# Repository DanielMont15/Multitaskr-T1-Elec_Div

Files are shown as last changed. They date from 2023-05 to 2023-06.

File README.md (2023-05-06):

## Multitaskr-T1-Elec_Div
# Electronics Division  
ECAD and documentation repository for everything electronics related to Rotational &amp; Controlled Mechanism and transmission system for camera scanner project.

# Abstract
Among the services offered by Multitaskr, a 3D manual scanning of rooms with a camera is performed. With the purpose of improving processes, the automation of this process is proposed by developing a mobile and foldable platform that allows modifying the Pitch and Yaw position (in a range of 360 and -45 to 45, respectively) of the camera via a robotic system with 2 degrees of freedom.

The development considers the use of SCRUM methodology to keep track of the proposed objectives and detected failures; CAD and ECAD software (SolidWorks and Eagle); MATLAB for the design and tuning of the controller; TEC laboratories and other related facilities; as well as testing the system to identify areas of opportunity.

In order to achieve this goal, the process will last 10 weeks and will be divided into areas (Mechanics, Electronics, Control and Manufacturing) with the involvement of 8th semester students in Mechatronics with relevant experience in these areas. The testing phase is intended to ensure the delivery of a product according to the specifications.  

A functional prototype is expected to be delivered with the requirements established in the design process; as well as an "Engineering Manual" with CAD models, research processes, schematics, codes and operation guidelines along with the tests and areas of opportunity identified. 

It has been identified that the system can improve the accuracy and efficiency of the process, benefiting Multitaskr operationally and providing its clients with greater value in the services acquired.

# Objective of this repository
To track and mantain in a single platform all related documents in order to be able to replicate the project if needed. Expect to find:
* Entries to the Engineering Manual on the electronics subdivision and updates to said entries.
* ECAD files of the desgined circuits
* Diagrams/Drawings

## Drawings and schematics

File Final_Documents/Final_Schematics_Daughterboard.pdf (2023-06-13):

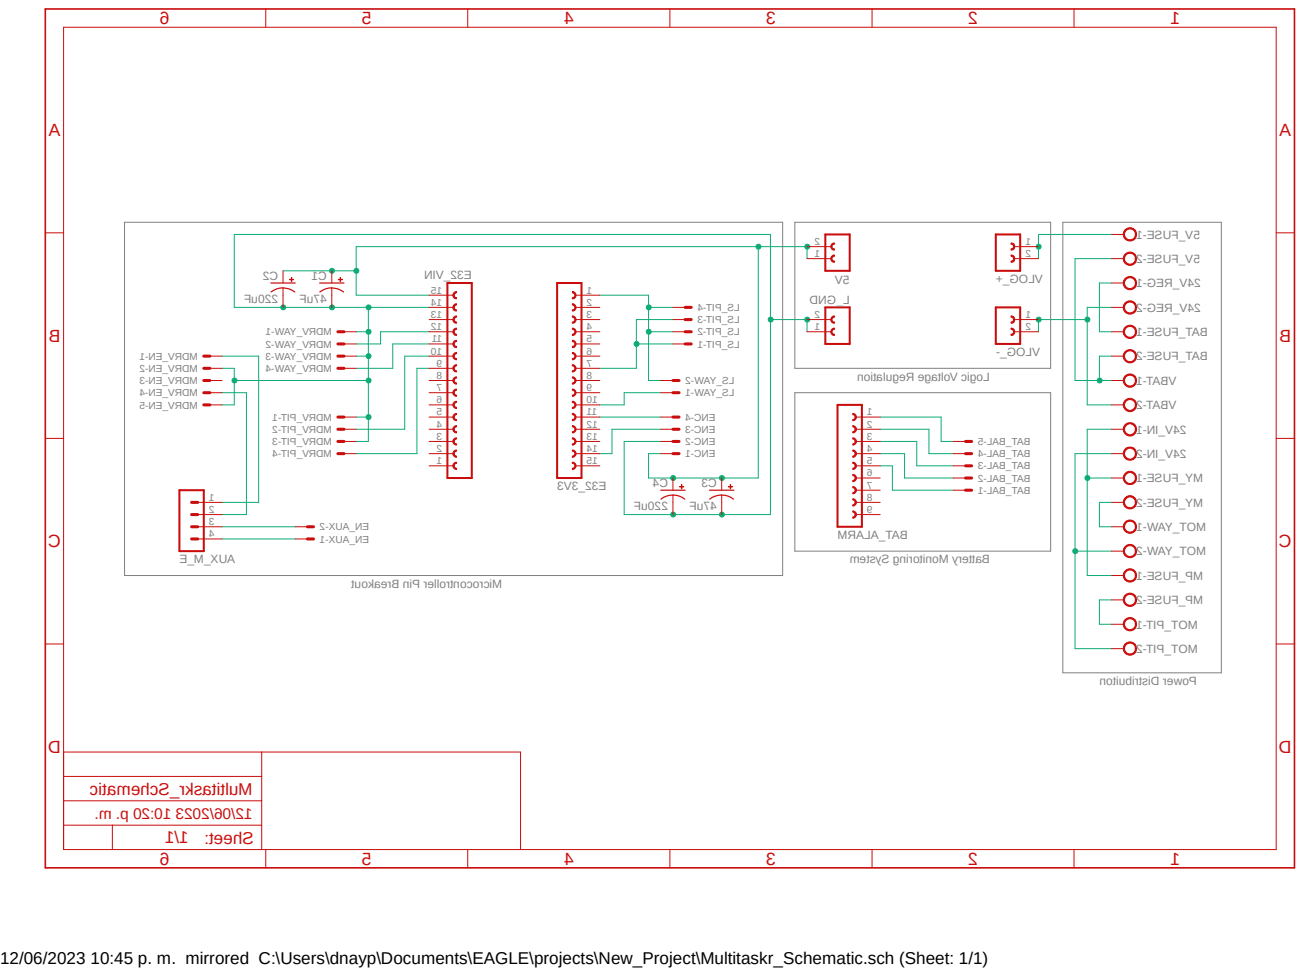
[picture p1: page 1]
Sheet:; Multitaskr_Schematic; 5V_FUSE-1; 5V_FUSE-2; 24V_REG-1; 24V_REG-2; BAT_FUSE-1; BAT_FUSE-2; VBAT-1; VBAT-2; MY_FUSE-1; MY_FUSE-2; MOT_YAW-1; MOT_YAW-2; MP_FUSE-1; MP_FUSE-2; MOT_PIT-1; MOT_PIT-2; 1 2 VLOG_+; 2 VLOG_- 1; L_GND; BAT_BAL-1; BAT_BAL-2; BAT_BAL-3; BAT_BAL-4; BAT_BAL-5; 1 2 3 4 5 6 7 8 9 BAT_ALARM; 15 C1 C2 E32_VIN; MDRV_PIT-1 MDRV_PIT-2 MDRV_PIT-3 MDRV_PIT-4; MDRV_YAW-1 MDRV_YAW-2 MDRV_YAW-3 MDRV_YAW-4; 1 2 3 4 AUX_M_E; EN_AUX-2; LS_YAW-2 LS_YAW-1; LS_PIT-1; LS_PIT-2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

Logic Voltage Regulation

EN_AUX-1 ENC-1 ENC-2 ENC-3 ENC-4 C3 C4

Battery Monitoring System

Microcontroller Pin Breakout

12/06/2023 10:45 p. m. mirrored C:\Users\dnayp\Documents\EAGLE\projects\New_Project\Multitaskr_Schematic.sch (Sheet: 1/1)

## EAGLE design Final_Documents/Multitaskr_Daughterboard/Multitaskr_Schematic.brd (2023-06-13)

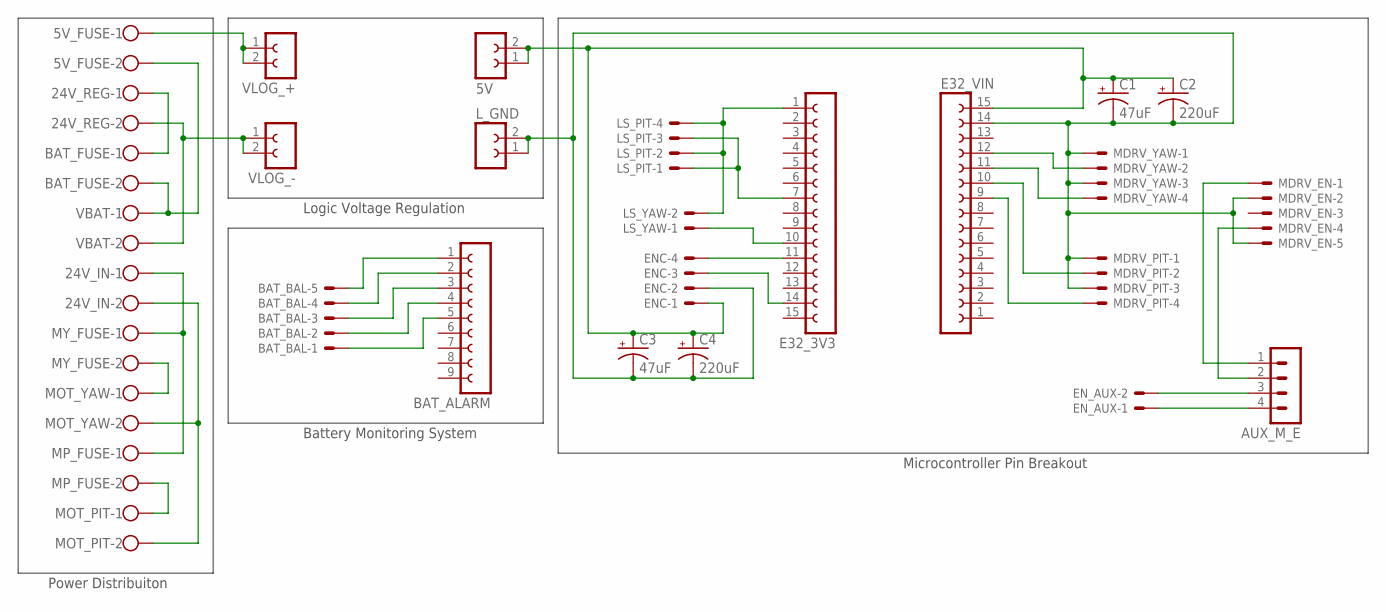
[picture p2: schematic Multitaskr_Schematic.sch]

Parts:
5V: FE05-1
5V_FUSE, 24V_IN, 24V_REG: SCREW_TERMINAL; FP_ST
AUX_M_E: MA04-1
BAT_ALARM: FE09-1; FE09
BAT_BAL: JST-XH-05-PIN-ROUND-PAD; JST-XH-05-PACKAGE-ROUND-PAD
BAT_FUSE: SCREW_TERMINAL; FP_ST
C1: 47uF; E2,5-7
C2: 220uF; E2,5RE
C3: 47uF; E2,5RE
C4: 220uF; E2,5-7
E32_3V3, E32_VIN: FE15-1; FE15
ENC: JST-XH-04-PIN-ROUND-PAD; JST-XH-04-PACKAGE-ROUND-PAD
EN_AUX: JST-XH-02-PIN-ROUND-PAD; JST-XH-02-PACKAGE-ROUND-PAD
LS_PIT: JST-XH-04-PIN-ROUND-PAD; JST-XH-04-PACKAGE-ROUND-PAD
LS_YAW: JST-XH-02-PIN-ROUND-PAD; JST-XH-02-PACKAGE-ROUND-PAD
L_GND: FE05-1
MDRV_EN: JST-XH-05-PIN-ROUND-PAD; JST-XH-05-PACKAGE-ROUND-PAD
MDRV_PIT: JST-XH-04-PIN-ROUND-PAD; JST-XH-04-PACKAGE-ROUND-PAD
MDRV_YAW: JST-XH-04-PIN-ROUND-PAD; JST-XH-04-PACKAGE-ROUND-PAD
MOT_PIT: SCREW_TERMINAL; FP_ST
MOT_YAW: SCREW_TERMINAL; FP_ST
MP_FUSE: SCREW_TERMINAL; FP_ST
MY_FUSE: SCREW_TERMINAL; FP_ST
VBAT: SCREW_TERMINAL; FP_ST
VLOG_+: FE05-1
VLOG_-: FE05-1

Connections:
1S: BAT_ALARM.2, BAT_BAL.4
2S: BAT_ALARM.3, BAT_BAL.3
3S: BAT_ALARM.4, BAT_BAL.2
3V3: E32_3V3.1, LS_PIT.2, LS_PIT.4, LS_YAW.2
4S: BAT_ALARM.5, BAT_BAL.1
5V: 5V.1, 5V.2, C1.+, C2.+, C3.+, C4.+, E32_VIN.15, ENC.1
24V: 24V_IN.1, MP_FUSE.1, MY_FUSE.1
-S: BAT_ALARM.1, BAT_BAL.5
BAT+: 5V_FUSE.2, BAT_FUSE.2, VBAT.1
BAT-: 24V_REG.2, VBAT.2, VLOG_-.1, VLOG_-.2
ENA_MOT_PIT: AUX_M_E.1, MDRV_EN.1
ENA_MOT_Y: AUX_M_E.2, MDRV_EN.4
EN_DIR: AUX_M_E.4, EN_AUX.1
EN_PGO: AUX_M_E.3, EN_AUX.2
ESP_SCL: E32_3V3.14, ENC.3
ESP_SDA: E32_3V3.11, ENC.4
FUSE_P: MOT_PIT.1, MP_FUSE.2
FUSE_REG: 24V_REG.1, BAT_FUSE.1
FUSE_Y: MOT_YAW.1, MY_FUSE.2
LS_PITCH: E32_3V3.7, LS_PIT.1, LS_PIT.3
LS_YAW: E32_3V3.10, LS_YAW.1
LV+: 5V_FUSE.1, VLOG_+.1, VLOG_+.2
L_GND: C1.-, C2.-, C3.-, C4.-, E32_VIN.14, ENC.2, L_GND.1, L_GND.2, MDRV_EN.2, MDRV_EN.5, MDRV_PIT.1, MDRV_PIT.3, MDRV_YAW.1, MDRV_YAW.3
M_GND: 24V_IN.2, MOT_PIT.2, MOT_YAW.2
PITCH_DIR: E32_VIN.10, MDRV_PIT.2
PITCH_PUL: E32_VIN.9, MDRV_PIT.4
YAW_DIR: E32_VIN.12, MDRV_YAW.2
YAW_PUL: E32_VIN.11, MDRV_YAW.4

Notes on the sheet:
Power Distribuiton
Logic Voltage Regulation
Battery Monitoring System
Microcontroller Pin Breakout

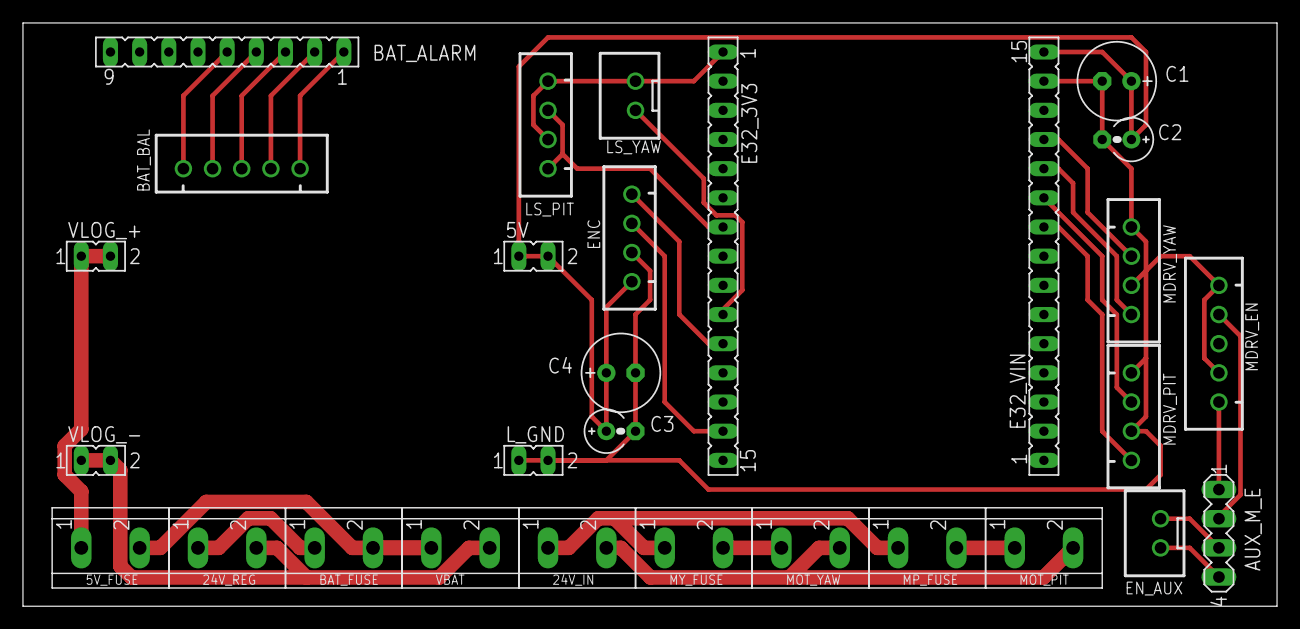
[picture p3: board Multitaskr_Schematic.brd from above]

Board: 2 copper layers, 109.2 x 50.8 mm, 29 parts (0 on the bottom side), 28 nets.

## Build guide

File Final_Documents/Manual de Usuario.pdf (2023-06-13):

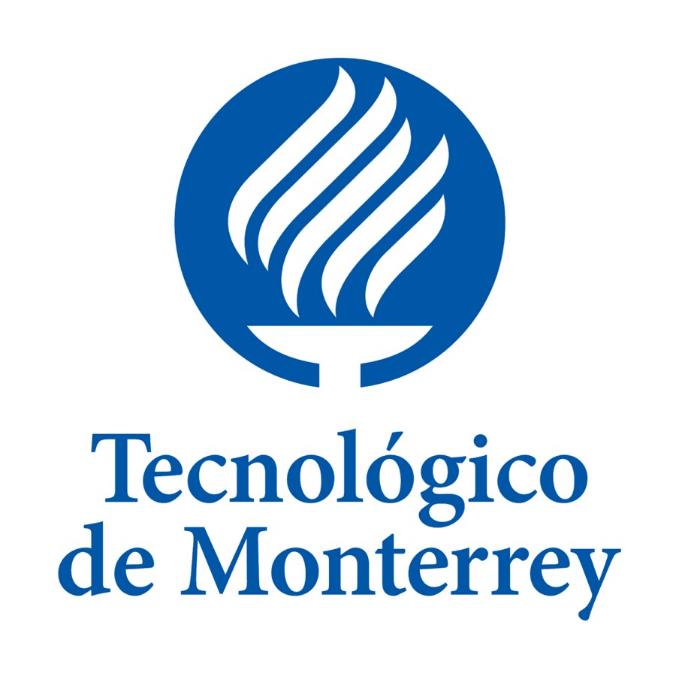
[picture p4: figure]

# Manual de Usuario – Rotational & Controlled Mechanism and transmission system for camera scanner

Diseño e implementación de sistemas mecatrónicos MR3002B

Grupo 501

Carlos Daniel López Montero - A01024473

07 de junio 2023

Instituto Tecnológico y de Estudios Superiores de Monterrey Campus Monterrey

Manual de Usuario – Rotational & Controlled Mechanism and transmission system for camera scanner

## Contenido

### Operación del tripie Plegado

Para conveniencia del usuario, el sistema presenta un tripie plegable. Para reducir este, es necesario tomar el elemento central del tripie y deslizarlo hacia la parte superior del sistema. A la vez, se puede apoyar de llevar cada una de las patas del tripie al centro del mismo. Al hacerlo, el sistema se colapsará, facilitando así el transporte de este.

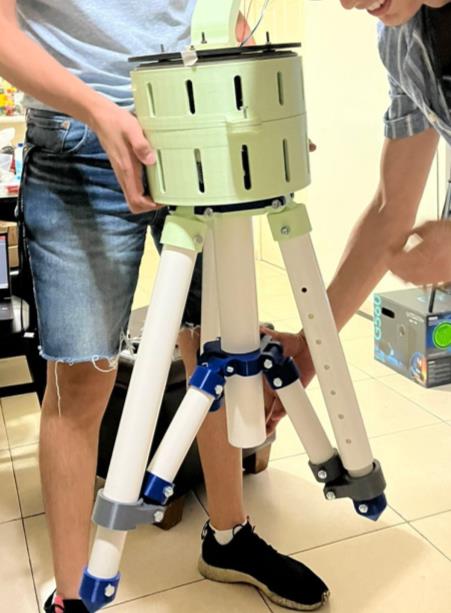
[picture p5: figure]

Ilustración 1 Colapse del tripie

### Ajuste de altura

El usuario cuenta con la posibilidad de ajustar la altura del sistema por medio del mecanismo de ajuste de altura en cada una de las patas del tripie. Para hacer uso de este, es necesario primero presionar el botón verde que se encuentra al costado de cualquiera de las patas del tripie. Al presionarlo, se liberará el sistema de ajuste, lo cual permitirá al usuario ya sea extender o retraer la tubería interna del sistema hasta la altura deseada. El sistema ofrece un ajuste total que va desde los 90 cm de altura hasta los 110 cm, haciendo uso de un sistema de agujeros de altura. Es indispensable cerciorarse que el botón verde vuelva a retraerse en alguno de los múltiples agujeros de altura del sistema. Se tiene que repetir este proceso otras dos veces con las patas faltantes para que el sistema termine con la altura ajustada de manera correcta.

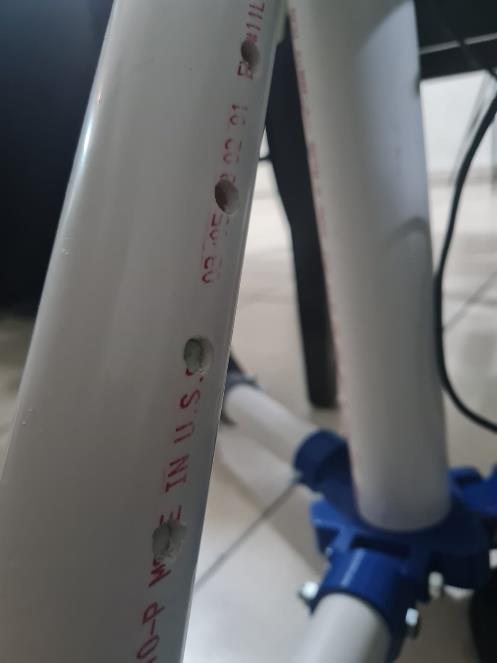
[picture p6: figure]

Ilustración 2 En la imagen se puede observar el botón verde del mecanismo de ajuste

Advertencia: Al ajustar la altura, es necesario que el botón verde del sistema de ajuste siente de manera correcta en los agujeros de ajuste. De no ser así, no colocar el sistema sobre el suelo, ya que existe riesgo de colapso.

### Acceso a la electrónica

Para poder obtener acceso a los elementos electrónicos del sistema, es necesario desmontar la parte superior de la caja principal del sistema. Hacer esto es sencillo; únicamente es necesario desatornillar los tres tornillos de ajuste que se encuentran al costado del sistema. Al hacerlo, se podrá levantar la parte superior del sistema con sumo cuidado. A partir de eso, será necesario desconectar la batería del sistema, los motores, encoder y limit switch para poder hacer la separación completa del sistema.

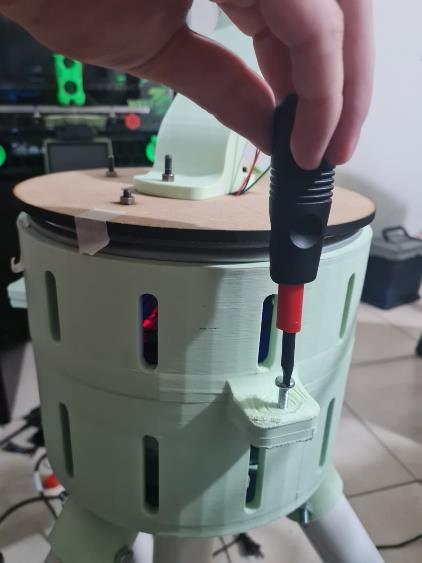
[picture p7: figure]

Ilustración 3 Tornillo para acceder a la electrónica

### Sección de electrónica Introducción

En esta sección del manual se explicará el funcionamiento y componentes que componen la PCB del proyecto, el cual tiene como objetivo principal simplificar las conexiones y proveer cierta protección (por el momento de sobrecarga) de los componentes. Adicionalmente se proveerá información sobre los pines y diagramas de conexión para simplificar el mantenimiento del prototipo y la primera puesta en marcha.

### Instrucciones de seguridad

Como cualquier dispositivo ingenieril, se recomienda ampliamente leer todas las instrucciones contenidas en este manual antes de realizar modificaciones u operar el dispositivo. Así mismo, aunque se esté trabajando con sistemas DC de bajo voltaje, se recomienda llevar a cabo medidas de seguridad/protección estándar debido al amperaje con el que trabaja el sistema.

a) Antes de realizar alguna modificación a las conexiones o componentes (sea retirar o añadir/desconectar o conectar/reemplazar algún componente) de la PCB se requiere que la fuente de alimentación se encuentre desconectada.
b) Se recomienda evitar golpes o cualquier daño físico a los componentes de la PCB y fuente de alimentación.
c) Por la naturaleza de la construcción de la PCB, se recomienda que se aíslen o protejan las conexiones realizadas, especialmente aquellas en la parte posterior de la placa.
d) No realizar modificaciones sin consultar los diagramas de conexión mostrados en este manual.
e) Cuidar la polaridad de los componentes eléctricos; aunque los reguladores de voltaje proveen protección contra inversión de voltaje y sobre corriente, se recomienda verificar que la conexión de estos y demás componentes sea checada para evitar daños. Se recuerda al usuario que estas protecciones son más de “cortesía” que protecciones debidamente diseñadas y consideradas en el desarrollo eléctrico del sistema, por lo que se debe prestar especial atención en este aspecto.
f) Evitar realizar mucha fuerza sobre la placa, conectores o componentes ya que esto podría dañarlos. De igual forma se recomienda evitar cualquier tipo de daño físico a la placa
g) Prestar atención en caso de percibir olor a quemado o sentir que algún cable, conexión o componente eléctrico se encuentre anormalmente caliente. En caso de que algún componente se encuentre caliente se recomienda dejarlo enfriar antes de manipularlo.
h) Se recomienda prestar atención a los calibres y polarización de los cables al momento de cablear el sistema; así mismo se recomienda realizar una inspección visual del material aislante de estos y que las conexiones se encuentren realizadas de manera correcta antes de prender ele sistema.
i) Verificar que ninguna conexión esté suelta o que pueda provocar algún corto en el sistema.
j) Verificar el estado físico de los fusibles y su conexión antes de prender el sistema.
k) El sistema está diseñado para recibir alimentación mediante baterías Li-Po o Li-Ion de máximo 4S o 14.8V nominales/16.6V máximo. En caso de requerir alimentar el sistema con algún otro tipo de batería se recomienda que este tenga su propio BMS, sistema de monitoreo de nivel de carga, conector XT60 y que entregue un voltaje máximo de 20V a 24V con un amperaje mínimo de 11 A para garantizar el funcionamiento del sistema. El cambio de las especificaciones de alimentación del sistema no es recomendable y esta acción implica que el usuario debe asumir completa responsabilidad de asegurarse que el sistema de regulación de voltaje y especificaciones de los fusibles sean debidamente revisados para garantizar el correcto funcionamiento del sistema. Como dato adicional, se establece que el sistema hace un Step Up de voltaje para los componentes motrices y un Step Down para los componentes lógicos, se recomienda mantener esta configuración para aprovechar al máximo el rango de voltaje de la batería empleada.
l) El sistema está equipado con una alarma de bajo voltaje para la fuente de alimentación, es recomendable parar la operación del sistema y realizar el cambio de la fuente en cuanto la alarma se escuche para evitar daños a los componentes eléctricos y a la fuente.
m) El sistema eléctrico del mecanismo no cuenta con ninguna protección contra agua y polvo, por lo que se recomienda evitar el contacto con la PCB o fuente de alimentación.

n) Evitar estar cerca de sustancias inflamables al momento de conectar o desconectar la fuente de alimentación debido a que se podrían presentar chispas.

### Familiarización con la PCB

A continuación, se muestra una imagen del diseño actual de la PCB, así como un diagrama de los arneses de distribución de potencia utilizados en este prototipo. Cabe recalcar que, aunque la PCB cuente con las borneras de distribución de potencia, la distribución de potencia se realiza por medio de los arneses debido a complicaciones en la manufactura de la PCB; el uso de estos arneses no implica una reducción en el funcionamiento del sistema ni una reducción en la flexibilidad, reparabilidad o facilidad de conexiones.

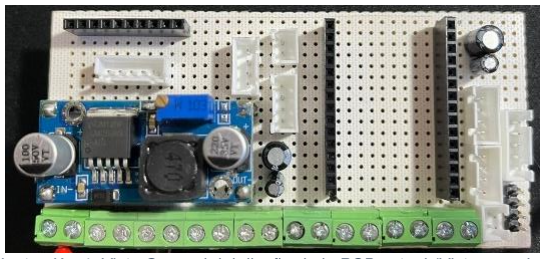
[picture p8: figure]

Ilustración 4. Vista General del diseño de la PCB actual (Vista superior)

Para facilitar la familiarización de la PCB al usuario, la misma se ha dividido en las siguientes secciones.

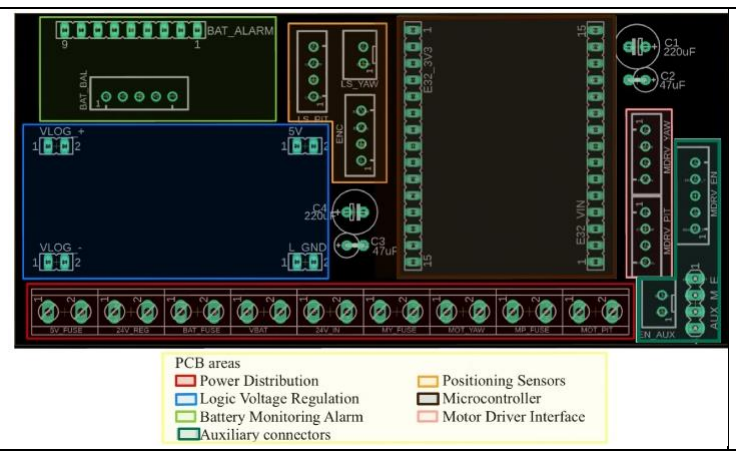
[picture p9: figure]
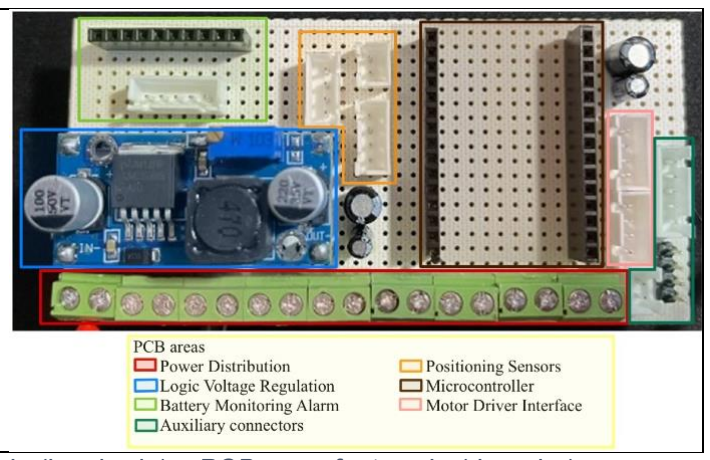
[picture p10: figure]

Ilustración 5. Zonas funcionales de la PCB diseñada (izquierda) y PCB manufacturada (derecha)

A continuación, se muestran los arneses con sus componentes.

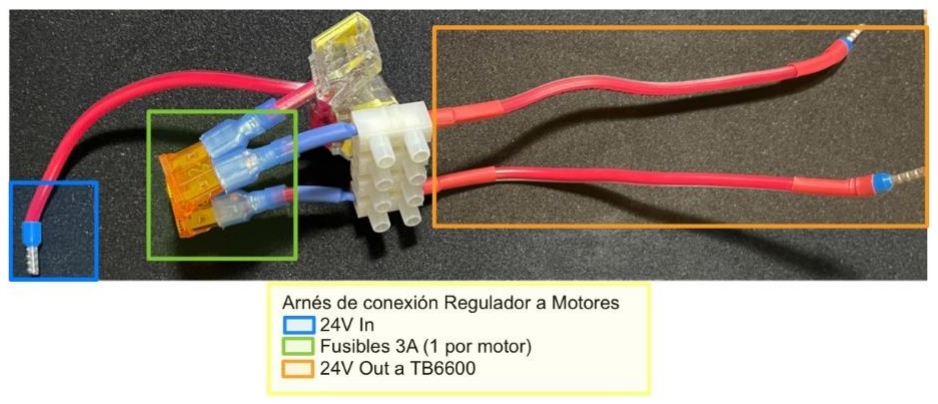
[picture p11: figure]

Ilustración 6. Arnés de conexión regulador-TB6600 Positivo (Arnés R2MP).

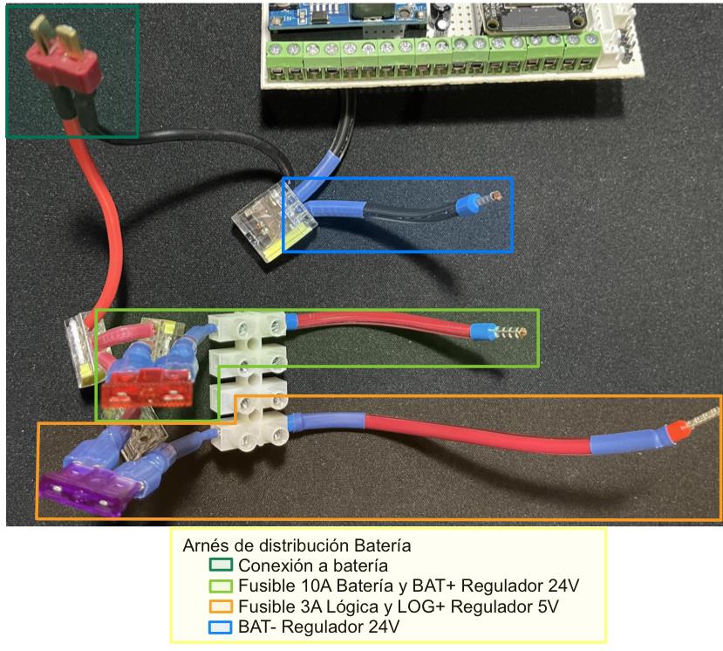
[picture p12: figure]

Ilustración 7. Arnés distribuidor batería-reguladores (Arnés B2R).

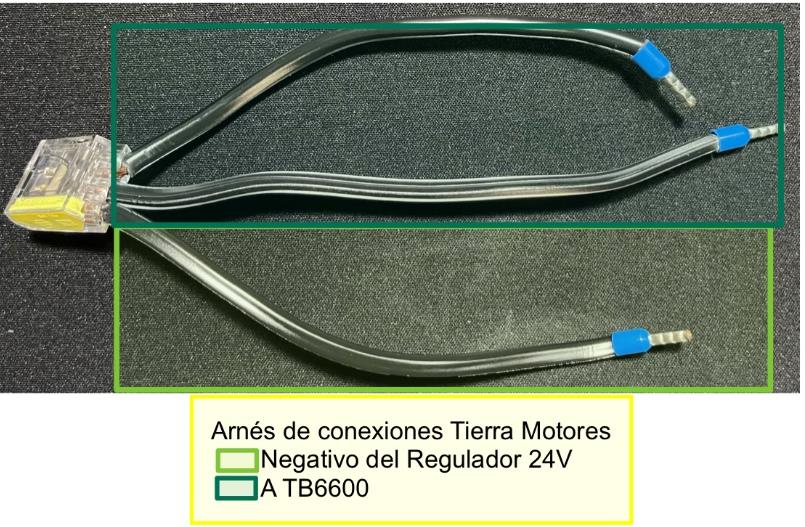
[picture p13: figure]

Ilustración 8. Arnés de conexión regulador-TB6600 negativo. (Arnés R2MN)

Finalmente, se listan los componentes necesarios

Componente | Cantidad
PCB (con Arnés B2R pre soldado) | 1
Fusible Automotriz 10A | 1
Fusible Automotriz 3A | 1
Arnés R2MP | 1
Fusible Automotriz 5A | 2
Arnés R2MN | 1
ESP32 | 1
TB6600 | 2
Elevador de Voltaje Boost 400W 15A | 1
LM2596 Regulador Step Down 25W 3A | 1

Motores 42-40 NEMA17 | 2
Encoder Magnético AS5600 | 1
Limit Switch | 1
Batería 4S5P (18650 Cells) | 1
Checador de Baterías LIPO | 1
Tabla 1. Componentes electrónicos necesarios para la conexión

### Instalación y conexiones de la PCB

Antes de realizar las conexiones, se recomienda asegurar que tanto el regulador LM2569 y el ESP32 estén instalados de forma correcta tomando como referencia la siguiente ilustración.

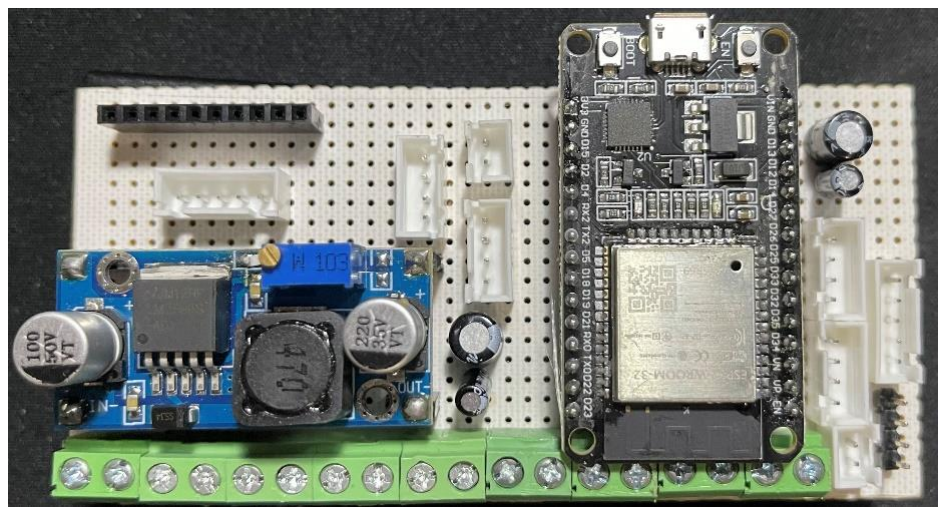
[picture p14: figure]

Ilustración 9. Orientación correcta del regulador y ESP32 instalados en la PCB

A continuación, se muestran diagramas generales de conexión de los a la PCB.

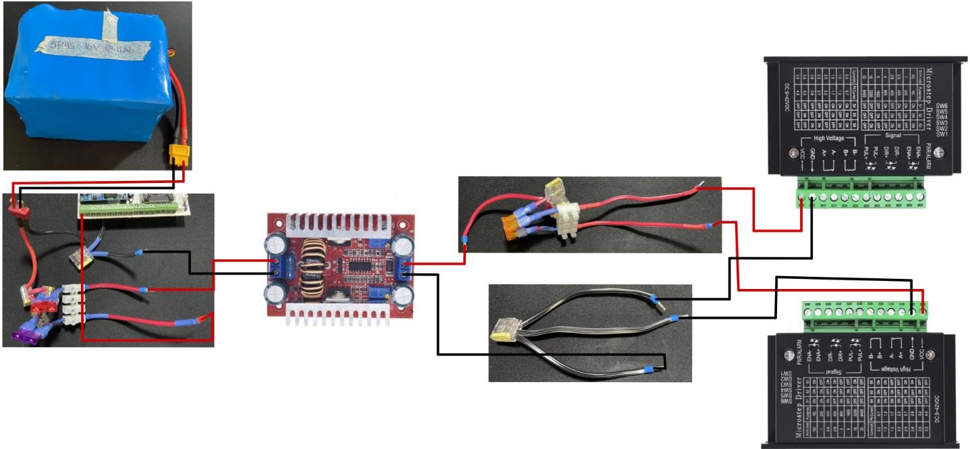
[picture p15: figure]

Ilustración 10. Diagrama general de conexiones de alimentación a la PCB

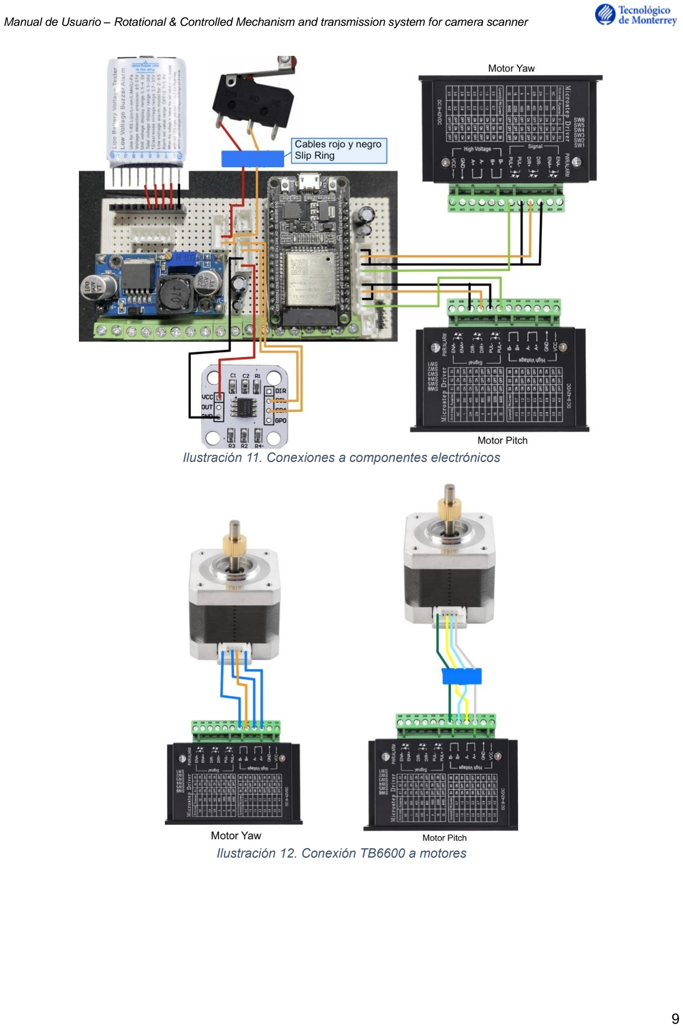
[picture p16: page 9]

Ilustración 11. Conexiones a componentes electrónicos

Ilustración 12. Conexión TB6600 a motores

### Funcionamiento de la aplicación

Para el funcionamiento de la aplicación, es necesario conectarse a la red dada por el ESP32:

1. Entrar a los ajustes de conexión de su teléfono,
2. Conectarse a la red ESP32 con la contraseña “12345678”
3. Una vez conectado, entrar al navegador de internet de su preferencia
4. En la barra del navegador escribir la IP “192.168.4.1” al hacer esto la aplicación se proyectará en la pantalla de su celular.

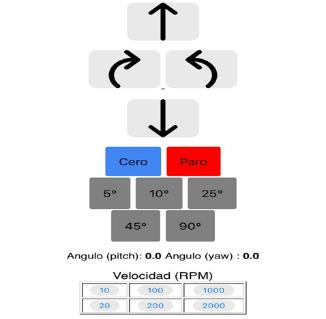
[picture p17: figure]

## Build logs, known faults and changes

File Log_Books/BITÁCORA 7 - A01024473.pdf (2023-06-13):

## BITÁCORA #7

Nombre: Carlos Daniel López Montero | Mat: A01024473
Socio Formador: Multitaskr | Profesor coordinador: Hilda Fumiko Monnier Inukai
Proyecto: Rotational & Controlled Mechanism and transmission system for camera scanner
Número de integrantes en el equipo: | 4
Fecha: 23/05/2023 | Semana # 7 | Del lunes 15/05/23 | Al viernes 19/05/23
ACTIVIDAD REALIZADA | # horas dedicadas
Describa brevemente las actividades realizadas en la semana (agregar renglones de ser necesario) | Act 1. Impresión de soportes encoders | 3
| Act 2. Compra de materiales para triple | 6
| Act 3. Lluvia de ideas interfaz de control HTML y secuencia de movimiento | 2
| Act 4.
Cuál fue tu contribución personal al avance del reto durante esta semana | Act 1. Preparación del archivo de impresión de los soportes de los encoders Act 2. Elaboración del esquemático electrónico para generar el PCB Act 3. Elaboración del diseño de la PCB Se realizaron ajustes en los cálculos realizados | Act 1. 0.5 horas Act 2. 2 horas Act3. 5 horas
TOTAL DE HORAS DEDICADAS EN LA SEMANA | | Activas: 15.5 En espera (impresión): 3 Totales: 18.5
¿Se avanzó en el reto conforme estaba planeado? | SI / NO ¿Por qué? Si, debido a que se está por finalizar la sección de electrónica (sin contar pruebas)
¿Qué requieres y de parte de quién, para tener un mejor avance en el reto? | Por el momento no se requiere de información adicional
Actividades pendientes de realizar la PRÓXIMA SEMANA | Ver viabilidad sobre la fabricación de la PCB a mano en placas fenólicas perforadas o mediante proceso químico

NO LLENAR (ESPACIO EXCLUSIVO PARA EL PROFESOR EVALUADOR) Nombre del profesor
¿Las actividades presentadas reflejan el número de horas de trabajo en el reto reportadas por el alumno? | SI / NO ¿Por qué?

Que evaluación le asignarías al avance del alumno en la semana, considera tanto las actividades realizadas, como el tiempo dedicado. (escala de 0 a 10)

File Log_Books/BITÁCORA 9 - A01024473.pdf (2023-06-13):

## BITÁCORA #9

Nombre: Carlos Daniel López Montero | Mat: A01024473
Socio Formador: Multitaskr | Profesor coordinador: Hilda Fumiko Monnier Inukai

Proyecto: Rotational & Controlled Mechanism and transmission system for camera scanner

Número de integrantes en el equipo: | 4
Fecha: 6/06/2023 | Semana # 9 | Del lunes 29/05/23 | Al viernes 02/06/23
ACTIVIDAD REALIZADA | # horas dedicadas
Describa brevemente las actividades realizadas en la semana (agregar renglones de ser necesario) | Act 1. Impresión de repuesto caja de engranes | Preparación: .5 horas Impresión: 2 horas
| Act 2.
| Act 3.
| Act 4.
Cuál fue tu contribución personal al avance del reto durante esta semana | Act 1. Corrección del primer prototipo de la PCB/Manufactura del segundo prototipo de la PCB Act 2. Pruebas de conexión de los componentes a la PCB Act 3. Condensado de la documentación del área de Electronica y propuesta de pruebas | Act 1. 8 horas Act 2. 3 horas Act 3. 8 horas
TOTAL DE HORAS DEDICADAS EN LA SEMANA | | Activas: 19.5 En espera (impresión): 2 Totales: 21.5

¿Se avanzó en el reto conforme estaba planeado?

SI / NO ¿Por qué?

Si, debido a que la segunda revisión de la PCB funciona conforme a lo esperado

¿Qué requieres y de parte de quién, para tener un mejor avance en el reto? | Por el momento no se requiere de información adicional
Actividades pendientes de realizar la PRÓXIMA SEMANA | Condensar la documentación de electrónica para la entrega de la evidencia 3. Elaborar manual de la PCB

NO LLENAR (ESPACIO EXCLUSIVO PARA EL PROFESOR EVALUADOR)

Nombre del profesor

¿Las actividades presentadas reflejan el número de horas de trabajo en el reto reportadas por el alumno? | SI / NO ¿Por qué?

Que evaluación le asignarías al avance del alumno en la semana, considera tanto las actividades realizadas, como el tiempo dedicado. (escala de 0 a 10)

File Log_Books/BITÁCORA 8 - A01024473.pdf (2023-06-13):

## BITÁCORA #8

Nombre: Carlos Daniel López Montero | Mat: A01024473
Socio Formador: Multitaskr | Profesor coordinador: Hilda Fumiko Monnier Inukai
Proyecto: Rotational & Controlled Mechanism and transmission system for camera scanner
Número de integrantes en el equipo: | 4
Fecha: 30/05/2023 | Semana # 8 | Del lunes 22/05/23 | Al viernes 26/05/23
ACTIVIDAD REALIZADA | # horas dedicadas
Describa brevemente las actividades realizadas en la semana (agregar renglones de ser necesario) | Act 1. Impresión de las bases y brazo de soporte para el mecanismo. | Preparación: 1 hora Impresión: 60 horas
| Act 2. | 6
| Act 3. | 2
| Act 4.
Cuál fue tu contribución personal al avance del reto durante esta semana | Act 1. Elaboración del primer prototipo de la PCB | Act 1. 6 horas
TOTAL DE HORAS DEDICADAS EN LA SEMANA | | Activas: 7 En espera (impresión): 60 Totales: 67
¿Se avanzó en el reto conforme estaba planeado? | SI / NO ¿Por qué? Si, aunque cabe destacar que el resultado obtenido del primer prototipado de la PCB fue insatisfactorio y se necesita una segunda revisión
¿Qué requieres y de parte de quién, para tener un mejor avance en el reto? | Por el momento no se requiere de información adicional
Actividades pendientes de realizar la PRÓXIMA SEMANA | Rediseñar el esquemático y PCB para simplificar manufactura y eliminar posibles puntos de falla

NO LLENAR (ESPACIO EXCLUSIVO PARA EL PROFESOR EVALUADOR) Nombre del profesor
¿Las actividades presentadas reflejan el número de horas de trabajo en el reto reportadas por el alumno? | SI / NO ¿Por qué?

Que evaluación le asignarías al avance del alumno en la semana, considera tanto las actividades realizadas, como el tiempo dedicado. (escala de 0 a 10)

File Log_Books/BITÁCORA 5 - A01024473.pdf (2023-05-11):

## BITÁCORA #5

Nombre: Carlos Daniel López Montero | Mat: A01024473
Socio Formador: Multitaskr | Profesor coordinador: Hilda Fumiko Monnier Inukai
Proyecto: Rotational & Controlled Mechanism and transmission system for camera scanner
Número de integrantes en el equipo: | 4
Fecha: 09/05/2023 | Semana # 5 | Del lunes 1/05/23 | Al viernes 5/05r/23
ACTIVIDAD REALIZADA | # horas dedicadas
Describa brevemente las actividades realizadas en la semana (agregar renglones de ser necesario) | Act 1. Pruebas del mecanismo de rotación propuestas. Se probo la caja de engranaje con la base impresa y se comprobó su funcionamiento. Se tomo nota de modificaciones a tomar para mejorar el funcionamiento. | 5
| Act 2. Compra de materiales. Se compraron tornillos, placas de MDF y material para impresión 3D | 5
| Act 3.
| Act 4.

Cuál fue tu contribución personal al avance del reto durante esta semana

Act 1. Documentación del diseño de fuente de poder.
Se documento el diseño de la batería a usar y se realizaron los esquemáticos.
Act 2. Actualización de documentación de la sección eléctrica.
Se actualizaron los documentos de ingeniería y el registro en Jira de las actividades.
Act 3. Creación del GitHub de electrónica.
Se dió de alta el repositorio con toda la documentación del área de electrónica
Act 4. Impresión de la base para el dispositivo. Se preparó e imprimió el prototipo de la base. Act 5. Mantenimiento correctivo de la impresora.
Se comenzó a dar mantenimiento correctivo a la impresora debido a falla en el Hotend.

Act 1: 5

Act 2: 5

Act 3: 1.5

Act 4: .5
Tiempo de
impresión: 16

Act 5: 10 horas

TOTAL DE HORAS DEDICADAS EN LA SEMANA Activas: 32 En espera (impresión): 16 Totales: 48

¿Se avanzó en el reto conforme estaba planeado?

SI / NO ¿Por qué?
Si, debido a que se está avanzando conforme a lo planeado en cuanto a la sección de electrónica. Sin embargo, el mantenimiento correctivo de la impresora nos retrasó en la sección de manufactura y pruebas

¿Qué requieres y de parte de quién, para tener un mejor avance en el reto? | Por el momento solo se requiere confirmación de dudas en cuanto a la selección de alimentación y posible implementación del sistema a control remoto (sin depender de la aplicación)
Actividades pendientes de realizar la PRÓXIMA SEMANA | Redacción del reporte de selección de la interfaz de control. Ver viabilidad sobre la fabricación de una placa de circuitos propia. Redacción del reporte de selección de controlador de motor Diseño de los esquemáticos de la interfaz-placa de control

NO LLENAR (ESPACIO EXCLUSIVO PARA EL PROFESOR EVALUADOR) Nombre del profesor
¿Las actividades presentadas reflejan el número de horas de trabajo en el reto reportadas por el alumno? | SI / NO ¿Por qué?

Que evaluación le asignarías al avance del alumno en la semana, considera tanto las actividades realizadas, como el tiempo dedicado. (escala de 0 a 10)

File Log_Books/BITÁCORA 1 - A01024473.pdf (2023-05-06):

## BITÁCORA #1

Nombre: Carlos Daniel López Montero | Mat: A01024473 | .
Socio Formador: Multitaskr | Profesor coordinador: Elvira
Proyecto: Rotational & Controlled Mechanism and transmission system for camera scanner
Número de integrantes en el equipo: | 4
Fecha: 11/04/2023 | Semana # 1 | Del lunes 27/03/2023 | Al viernes 31/03/2023
¿Ya tuviste la sesión de arranque con el SOCIO FORMADOR? | | Si
ACTIVIDAD REALIZADA | # horas dedicadas
Describa brevemente las actividades realizadas en la semana (agregar renglones de ser necesario) | Act 1. - | 0
| Act 2. - | 0
| Act 3. - | 0
| Act 4. - | 0
Cual fue tu contribución personal al avance del reto durante esta semana | - | 0
TOTAL DE HORAS DEDICADAS EN LA SEMANA | | 0
¿Se avanzó en el Reto conforme estaba planeado? | SI / NO ¿Por qué? No, debido a que se presentó un período vacacional y la decisión del equipo fue retomar el trabajo después del mismo; además, el socio formador nos dijo que nos iba a proporcionar diseños e información relevante pero todavía no ha sido recibida
¿Qué requieres y de parte de quién, para tener un mejor avance en el reto? | Información técnica y requerimientos por parte del socio formador, así como historial ingenieril del proyecto.
Actividades pendientes de realizar la PRÓXIMA SEMANA | 1. Abstract Expo ingenierías 2. Estado del Arte y la Técnica 3. Definición de objetivos y calendarización 4. bitácora semana 2 ..

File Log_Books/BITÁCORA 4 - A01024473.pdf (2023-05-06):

## BITÁCORA #4

Nombre: Carlos Daniel López Montero | Mat: A01024473
Socio Formador: Multitaskr | Profesor coordinador: Hilda Fumiko Monnier Inukai
Proyecto: Rotational & Controlled Mechanism and transmission system for camera scanner
Número de integrantes en el equipo: | 4
Fecha: 02/05/2023 | Semana # 4 | Del lunes 24/04/23 | Al viernes 28/04/23
ACTIVIDAD REALIZADA | # horas dedicadas
| Act 1. Selección e impresión de la caja de engranes para la reducción del motor seleccionado. | 1.5 a la investigación 8 en la impresión
| Act 2. Compra de baleros y tornillería necesaria para poder ensamblar la caja. | 2.5
| Act 3. Ensamblado de la caja de engranes. En esta sección se rectificaron errores de impresión y se realizó el armado de la caja de engranajes para lograr su funcionamiento. Se encontraron complicaciones al momento de realizar esta actividad. | 12
| Act 4. Pruebas de la caja de engranes. En esta sección se encontraron problemas por parte de los componentes electrónicos del control del motor usados y la fuente de poder. Se plantea comprar los componentes definitivos la próxima semana. | 12
Cuál fue tu contribución personal al avance del reto durante esta semana | Documentación de la sección de selección de fuente de poder. Se estableció el camino a seguir para la construcción de la pila, así como las tecnologías a usar y cálculos preliminares/teóricos sobre la capacidad de esta. Se realizó mantenimiento correctivo (cambio de sistema de extrusión y corrección de bugs en firmware y SO de control) de la impresora 3D para garantizar su futuro funcionamiento en la etapa de manufactura. Lluvia de ideas sobre interfaz de control. (Se plantea escribir un reporte de este). | Documentación batería: 5 Mantenimiento correctivo: 4.5 Lluvia de ideas: .5
TOTAL DE HORAS DEDICADAS EN LA SEMANA | | Activas: 38 En espera (impresión): 8 Totales: 46

Describa brevemente las
actividades realizadas en la semana
(agregar renglones de ser
necesario)

¿Se avanzó en el reto conforme estaba planeado?

SI / NO ¿Por qué?
Si, debido a que se logró realizar las pruebas preliminares del motor y el sistema de reducción, así como se logró determinar el sistema a utilizar para alimentar el prototipo. Adicionalmente, se avanzó

| conforme a lo previsto en la lluvia de ideas o camino a tomar para la próxima semana
¿Qué requieres y de parte de quién, para tener un mejor avance en el reto? | Por el momento solo se requiere confirmación de dudas en cuanto a la selección de alimentación y posible implementación del sistema a control remoto (sin depender de la aplicación)
Actividades pendientes de realizar la PRÓXIMA SEMANA | Redacción del reporte de selección del microcontrolador. Redacción de un primer acercamiento a la interfaz de control Ver viabilidad sobre la fabricación de una placa de circuitos propia. Comenzar a ver la compra de los materiales necesarios para ensamblar la fuente de poder

NO LLENAR (ESPACIO EXCLUSIVO PARA EL PROFESOR EVALUADOR) Nombre del profesor
¿Las actividades presentadas reflejan el número de horas de trabajo en el reto reportadas por el alumno? | SI / NO ¿Por qué?

Que evaluación le asignarías al avance del alumno en la semana, considera tanto las actividades realizadas, como el tiempo dedicado. (escala de 0 a 10)

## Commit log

2023-05-06 Added Actividad 2.1. Definición de objetivos, justificación y resultados esperados
2023-05-09 Fixed Table 3 Information to reflect consuption from 2 motors
2023-05-10 Added Power Supply Engineering Manual entry
2023-05-10 Added Battery Schematics
2023-05-11 Added guide document for battery selection to be sent to Multitaskr/Fixed typos in other documents
2023-05-13 Added entry for voltage regulators and motor control selection
2023-05-18 Updated file structure naming/Added General Electrical Schematics to work on main PCB
2023-05-24 Added first iteration of the PCB schematics; to be cleaned to improve readibility
2023-05-24 Added first iteration of daughterboard .brd file; to be redesigned to reflect current component sizes and layouts of current prototype board
2023-05-29 Added modified daughterboard schematic pdf
2023-05-29 Added updated .brd files of PCB (normal version and mirrored version)
2023-06-13 Updated Log documents and schematics
2023-06-13 Added Final Documents (IEEE Design report, EAGLE Project Files, Schematics and PCB Reference PDFs, Instruction Manual)
    [Multitaskr_Schematic.brd, Multitaskr_Schematic.sch]
